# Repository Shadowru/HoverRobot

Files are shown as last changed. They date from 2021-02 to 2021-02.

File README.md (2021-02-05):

Робот из гироскутера
====================

### 1. [Список материалов](./BOM.md)

### 2. [Разбор гироскутера](./Disassembly.md)

### 3. [Подготовка деталей для сборки](./Preparations.md)

### 4. [Прошивка контроллера](./Firmware.md)

### 5. [Электрическая часть](./Electric_harness.md)

### 6. [Сборка](./Assembly.md)

### 7. [Установка ROS и запуск](firmware/README.md)

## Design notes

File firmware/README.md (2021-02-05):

Установка ROS велась с [чистого образа](https://developer.nvidia.com/jetson-nano-sd-card-image)

Все действия далее оформлены в отдельный скрипт : [install.sh](../scripts/install.sh)

### Убираем графику

```shell
sudo systemctl set-default multi-user.target
```

### Обновляем репозитории

```shell
sudo apt-get update
sudo apt-get upgrade
```

### Установка типовой конфигурации ROS
```shell
sudo sh -c 'echo "deb http://packages.ros.org/ros/ubuntu $(lsb_release -sc) main" > /etc/apt/sources.list.d/ros-latest.list'
sudo apt-key adv --keyserver 'hkp://keyserver.ubuntu.com:80' --recv-key C1CF6E31E6BADE8868B172B4F42ED6FBAB17C654
sudo apt-get update
sudo apt-get --yes install ros-melodic-desktop
```

### Создание ROS catkin среды

```shell
echo "source /opt/ros/melodic/setup.bash" >> ~/.bashrc
source ~/.bashrc
source /opt/ros/melodic/setup.bash

sudo apt-get --yes install python-rosdep python-rosinstall python-rosinstall-generator python-wstool build-essential
sudo rosdep init
rosdep update

mkdir -p ~/catkin_ws/src
cd ~/catkin_ws/
catkin_make
echo "source ~/catkin_ws/devel/setup.bash" >> ~/.bashrc
source ~/.bashrc
```

### Установка необходимых пакетов

```shell
sudo apt-get --yes install ros-melodic-cv-bridge ros-melodic-rosbridge-server ros-melodic-web-video-server libuvc-dev ros-melodic-uvc-camera ros-melodic-libuvc-camera ros-melodic-move-base ros-melodic-gmapping ros-melodic-robot-localization

sudo apt-get --yes install python-future

cd ~/catkin_ws/src/
git clone https://github.com/robopeak/rplidar_ros.git
git clone https://github.com/Shadowru/hoverboard_driver.git
git clone https://github.com/Shadowru/rosgolf_web_interface.git

sudo ln -s /usr/include/opencv4 /usr/include/opencv

cd ~/catkin_ws/
catkin_make
```

### Установка веб сервера

```shell
curl -sL https://deb.nodesource.com/setup_12.x | sudo -E bash -
sudo apt-get install --yes nodejs

cd ~/catkin_ws/src/rosgolf_web_interface/web_interface/
npm install rosnodejs express socket.io yargs
npm install
```

### Конфигурация

Настроить права :
```shell
sudo ~/catkin_ws/src/rosgolf_web_interface/script/setup_udev.sh
```

Отредактировать  ```~/catkin_ws/src/rosgolf_web_interface/launch/rosgolf_interface.launch```

Заменить имя СОМ порта для связи с платой на текущий в параметре 
```xml
<param name="uart" value="{имя СОМ порта}"/>
```
Пользователю под которым запускается ROS пакет должен быть доступен этот порт.  
Если используется Jetson Nano аппаратный ```/dev/ttyTHS1``` его надо освободить от системных служб

```shell
sudo systemctl stop nvgetty
sudo systemctl disable nvgetty
sudo udevadm trigger
sudo gpasswd --add rosgolf dialout
```

Заменить VID/PID в настройках камеры :
```xml
<param name="vendor" value="{VID}"/>
<param name="product" value="{PID}"/>
<param name="width" value="800"/>
<param name="height" value="600"/>
<param name="video_mode" value="mjpeg "/> <!-- or yuyv/nv12/mjpeg -->
<param name="frame_rate" value="30"/>
```
TODO: добавить скрипт для настройки камеры из режимов

### Запуск ROS сборки

roslaunch rosgolf_web_interface rosgolf_interface.launch

В браузере по адресу http://{IP адрес Jetson NANO}:8000/ должна быть страница с управлением роботом и видеопотоком

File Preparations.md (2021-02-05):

# Заготовка деталей

Необходимо вырезать из фанеры 4мм лобзиком, либо на станке :

3 детали

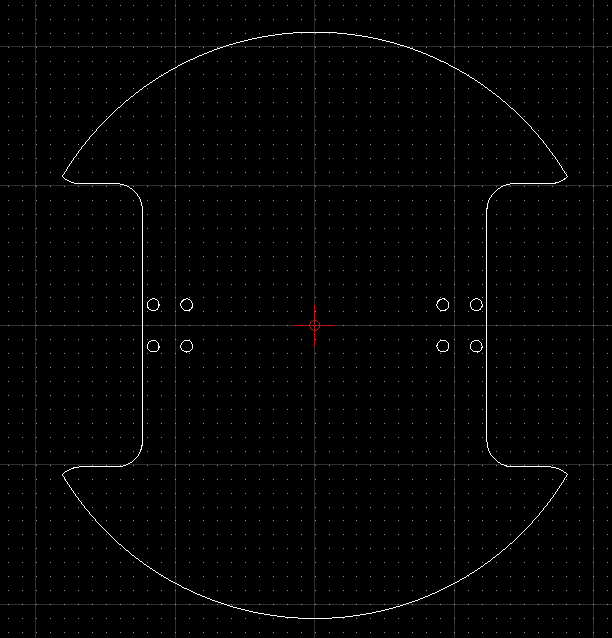
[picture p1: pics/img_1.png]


[Чертеж низа](./drawings/base_template.dxf) (Базируется на работе [Isabelle Simona](https://hackaday.io/project/158256-hoverbot))

2 детали по следующим чертежам
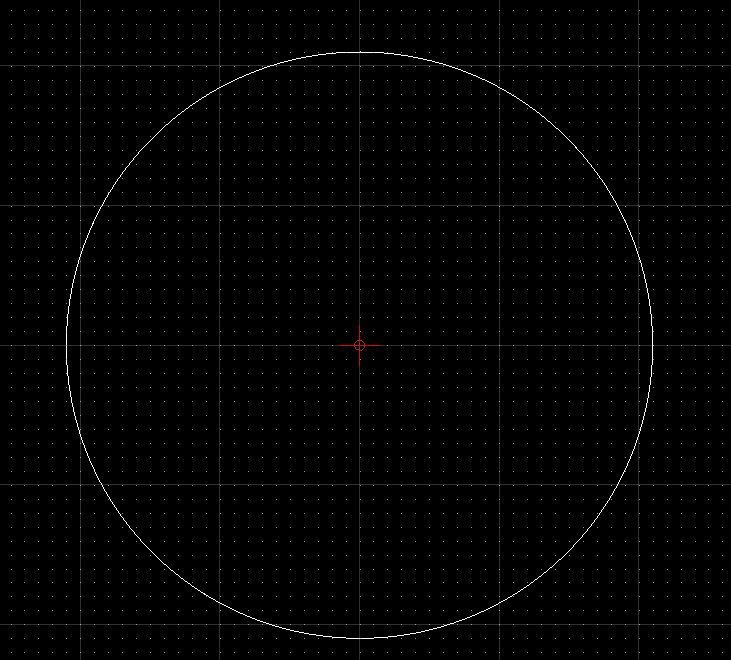
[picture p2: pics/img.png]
  
[Чертеж верха](./drawings/base_top.dxf)

Детали склеиваются по двое столярным ПВА клеем

[PIC]

Кроме этого понадобится брус 40х40 достаточной длины, что бы отпилить :

* 2 бруска по 145 мм
* 2 бруска по 110 мм

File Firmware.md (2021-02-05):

TODO: полное описание  

Windows
----------------------

* Запаять разъем на контроллер

* Подключить ST-LINK к контроллеру



* Установить [OpenOCD](https://gnutoolchains.com/arm-eabi/openocd/)

Подключить контроллер к батарее, нажать на кнопку включения питания и держать пока не прошьется.

* Запустить скрипт [upload-hoverboard.bat](./firmware/upload-hoverboard.bat) 

Если прошивка прошла с ошибкой:

[PIC]

* Запустить скрипт [unlock-hoverboard.bat](./firmware/unlock-hoverboard.bat)
* Запустить скрипт [upload-hoverboard.bat](./firmware/upload-hoverboard.bat) 

Linux
-------------------------
TODO:

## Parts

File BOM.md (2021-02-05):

BOM:

|Деталь  | Кол-во | Примечание |
|---|:---:|---:|
| Колесо 6.5'' | 2 | Есть в гироскутере |
| Крепежи колес | 2 | Есть в гироскутере |
| Контроллер гироскутера | 1 | Есть в гироскутере |
| Батарея гироскутера | 1 | Есть в гироскутере |
| Кнопка пуска | 1 | Есть в гироскутере |
| Разъем зарядки | 1 | Есть в гироскутере |
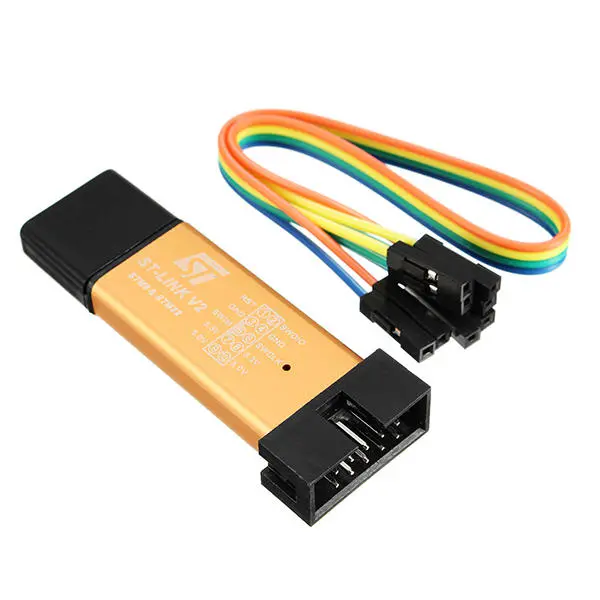
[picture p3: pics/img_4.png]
| ST-LINK адаптер| 1 |  |
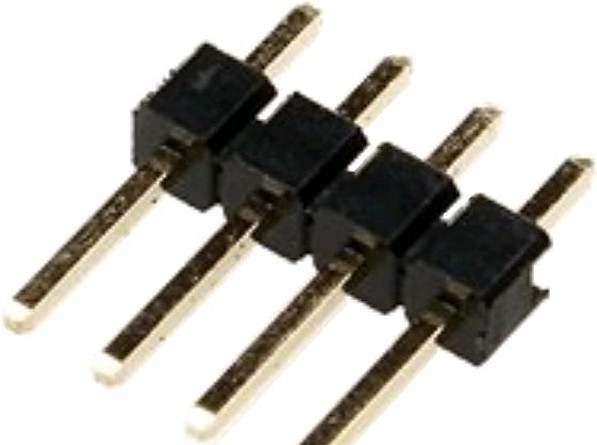
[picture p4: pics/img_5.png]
| Вилка штыревая 2.54мм 1х4| 1 |  |
| Болт М8х40 | 8 |  |
| Гайка М8 | 8 |  |
| Шайба М8 | 8 |  |
| Винт М4х20 | 10 |  |
| Винт М4х40 | 4 |  |
| Гайка М4 | 14 |  |
| Шайба М4 | 12 |  |
| Шурупы | 6 |  |
| Фанера 4мм шлифованная | около 0,5 м2 |  |
| Клей ПВА | около 50 гр |  |
| Брус 40х40 | около 1м |  |
| Jetson Nano | 1 |  |
| DC-DC адаптер 40V-5V 3A| 1 |  |
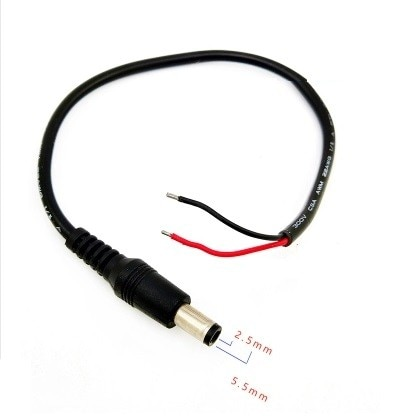
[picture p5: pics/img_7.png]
| Разъем 5.2 мм| 1 |  |
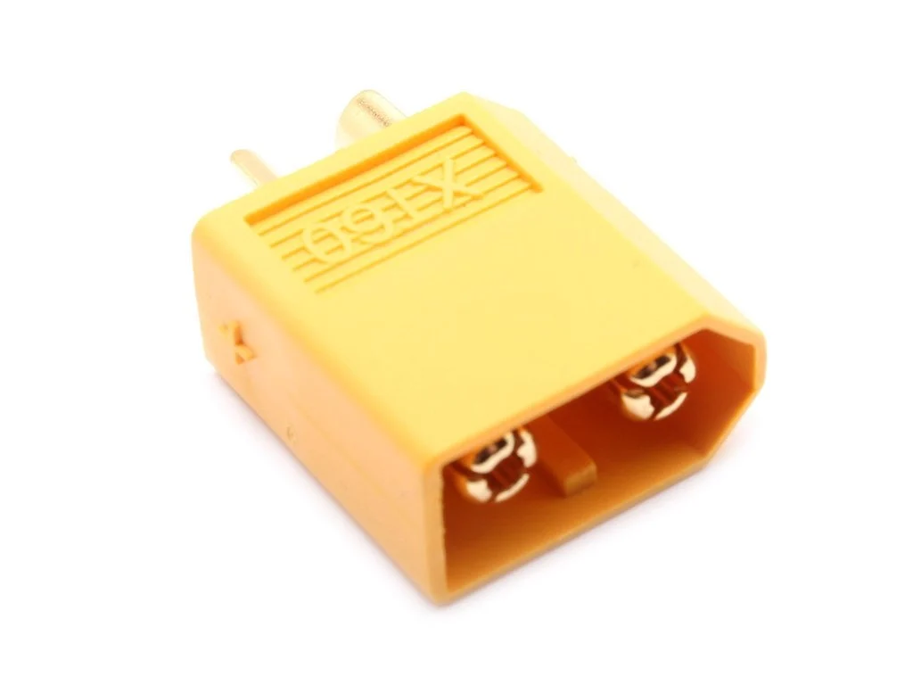
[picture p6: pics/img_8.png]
| Разъем XT60 розетка | 2 |  |
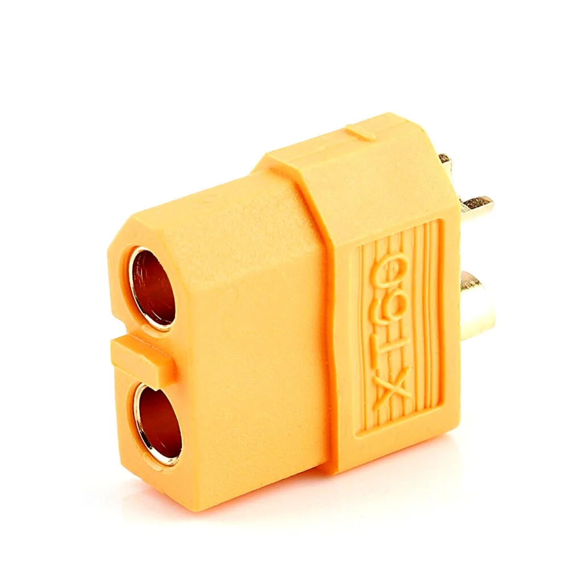
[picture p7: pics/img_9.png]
| Разъем XT60 вилка | 1 |  |

Опционально :

|Деталь  | Кол-во | Примечание |
|---|:---:|---:|
| Веб-камера | 1 |  |
| Лидар RPLidar A2 | 1 |  |

Кроме этого понадобится :
* Отвертка PH2
* Отвертка HEX6
* 3D принтер
* Паяльное оборудование - паяльник, олово, флюс
* Компьютер

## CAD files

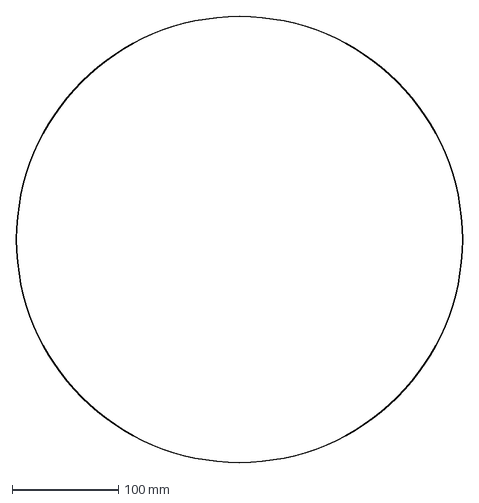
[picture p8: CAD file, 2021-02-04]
drawings/base_top.dxf
420.0 x 420.0 mm

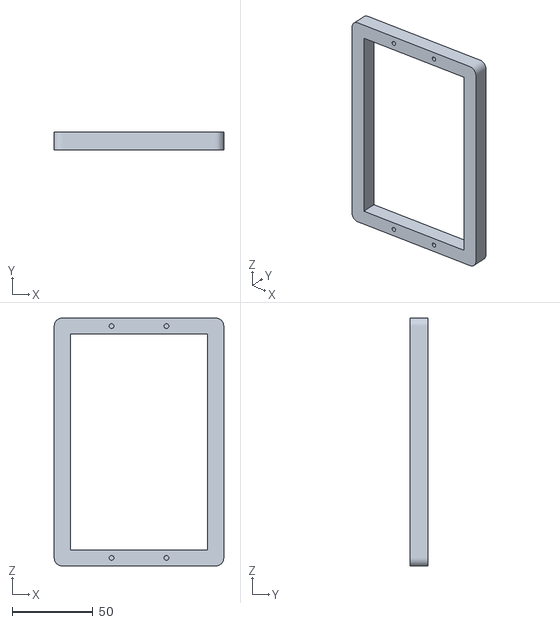
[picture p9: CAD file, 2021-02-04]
STL/BatteryHolder.stl
105.0 x 11.0 x 153.5

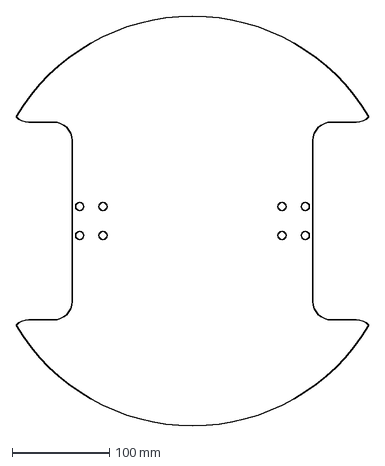
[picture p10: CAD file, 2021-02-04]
drawings/base_template.dxf
362.4 x 420.7 mm

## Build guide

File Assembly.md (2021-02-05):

### 2.2 Сборка низа

Используя 8 болтов М8х40 и крепежные пластины от гироскутера, устанавливаем колеса

[PIC]

Далее поддерживающие колеса :

Подробно тут :

(https://youtu.be/-oDFadHIRdk)

Максивально просто - высота от крепежа до точки касани должна быть 60 мм и должна быть площадка для крепления, а не 1 центральная ось.

Размечаем центральную линию, ставим колеса и размечаем точки крепления.
По намеченным точкам - высверливаем отверстия и ставим колеса на болты M4x20,
обязательно прокладывая шайбами место установки

2 бруска по 125 мм устанавливаются вдоль ниш колес и проклеиваются столярным ПВА клеем

[pic]

2 бруска по 110 мм устанавливаются на дальней стороне и проклеиваются столярным ПВА клеем

[pic]

Между брусками устанавливается контроллер

[pic]

Соединяются провода

[pic]

### 2.2 Установка батареи
Батарея устанавливается в держатель на болты М4х40 ??
[PIC]

Модель держателя взята отсюда : [M365 extra battery from hoverboard](https://www.thingiverse.com/thing:4254412)
и перевыложена локально : [STL файл держателя батареи](./STL/BatteryHolder.stl)

### 2.2 Установка крышки отсека

Оставшаяся деталь низа опиливается по синей линии
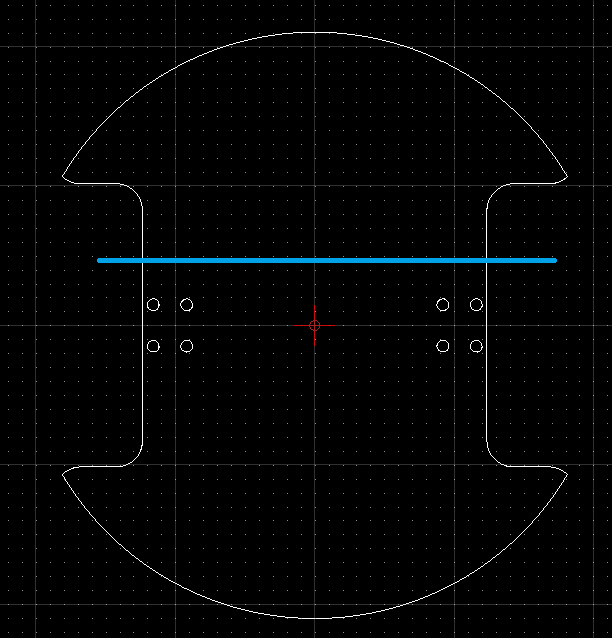
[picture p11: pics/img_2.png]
Крышка отсека крышка


Используя крепления для мебели все крепится на бруски

[pic]

### 2.2 Установка крышки робота

После того как все подогнано - шурупами закрепляются 2 бруска по 125 мм и 2 бруска по 110 мм

На бруски 110 мм устанавливаются петли, на

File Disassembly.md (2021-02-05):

## Разбор гироскутера

* Отвинтить болты отверткой PH2

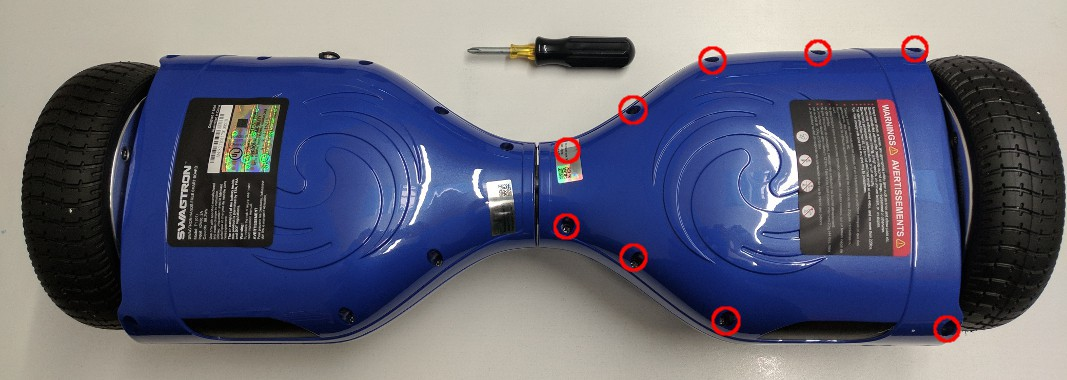
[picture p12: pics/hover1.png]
Гироскутер Гироскутер верхняя крышка


* Отвинтить болты отверткой PH2. Снять контроллер 
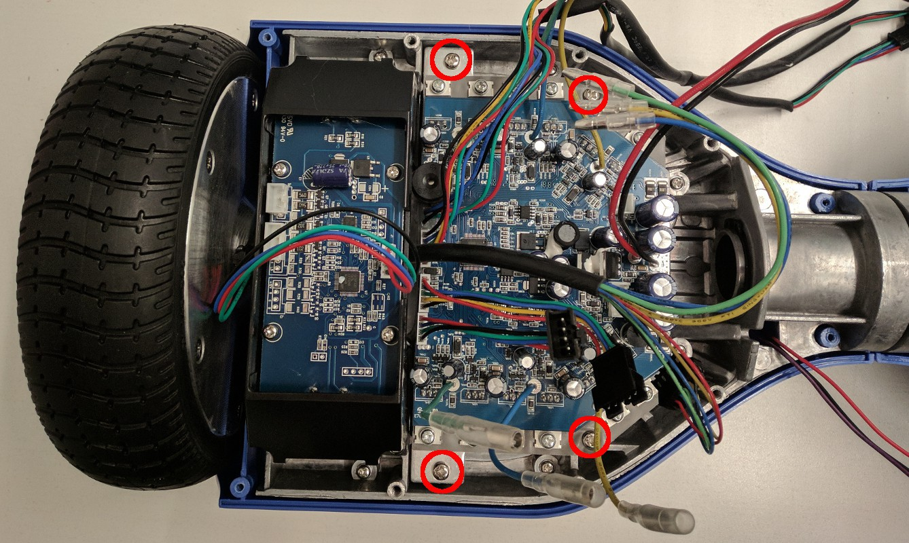
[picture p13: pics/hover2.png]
Гироскутер Гироскутер контроллер


* Снять боковые платы отверткой PH2  
* Болты колес откручиваются HEX 6mm  
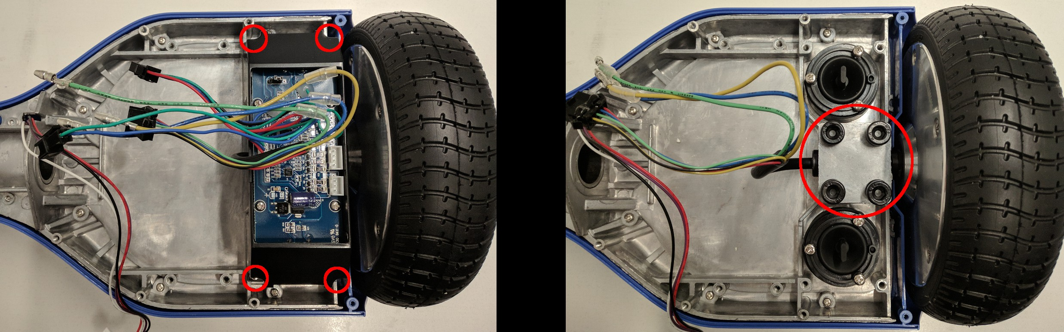
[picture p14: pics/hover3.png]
Гироскутер Гироскутер боковые платы и колеса


Снять кнопки пуска и разъем зарядки
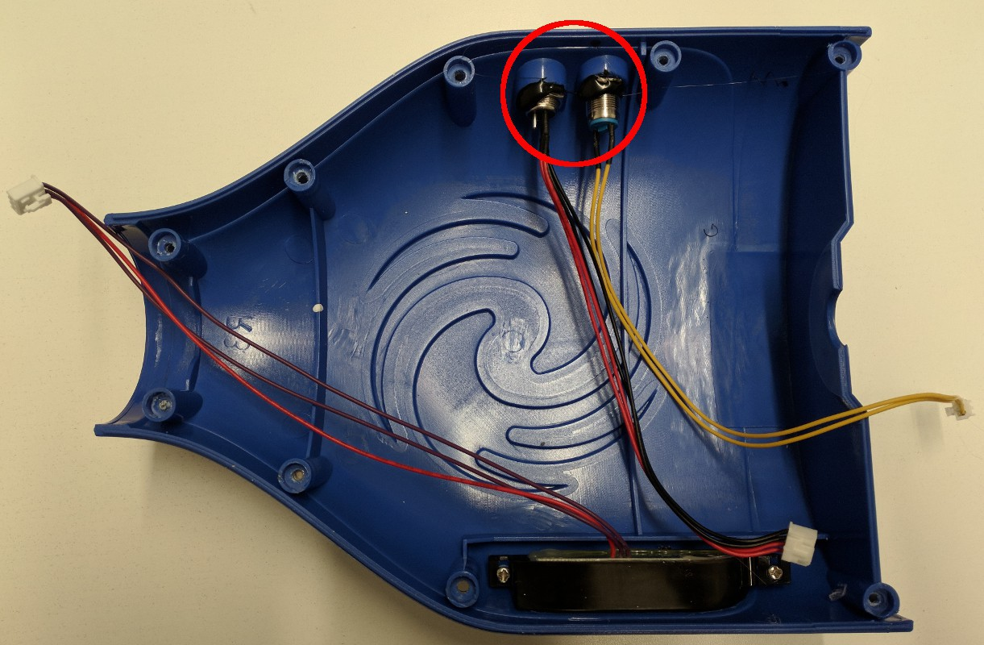
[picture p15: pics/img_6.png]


Вот то, что нужно будет для сборки робота :

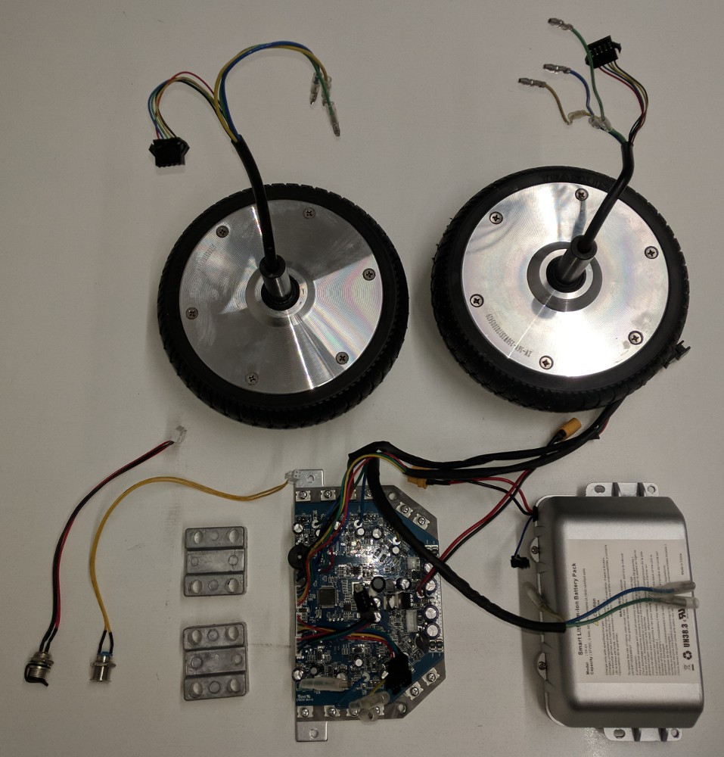
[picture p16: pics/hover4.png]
Гироскутер Гироскутер нужные части
